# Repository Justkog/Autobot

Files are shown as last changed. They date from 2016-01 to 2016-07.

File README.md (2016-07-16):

# Autobot
42 Project

This repo regroups code and design documents created to build a robot with 3 microphones constantly listening to the environment. 
On detection of a sound, the robot performs a triangulation to locate the source and then goes towards it. 

Usage of Arduino or any similar board was not allowed.

We used a PIC32MX programmed via MPLABX. 
The PCB design was performed with Altium.

This project is not actively maintained.

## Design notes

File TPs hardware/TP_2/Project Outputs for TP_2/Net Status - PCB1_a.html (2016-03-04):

Altium customize

# Net Status Report

Date | : | 3/4/2016
Time | : | 4:05:06 PM
Elapsed Time | : | 00:00:00
Filename | : | C:\Users\bocal\Desktop\Autobot\TP_2\PCB1_a.PcbDoc
Units | : | mmmils

Nets | Layer | Length
ALIM | Signal Layers Only | 22.066mm
BATTERY | Signal Layers Only | 5.3418mm
GND | Signal Layers Only | 232.2898mm
LED0 | Signal Layers Only | 31.5226mm
LED1 | Signal Layers Only | 33.7189mm
LED2 | Signal Layers Only | 36.8631mm
LED3 | Signal Layers Only | 41.149mm
MCLR | Signal Layers Only | 13.7259mm
NetC10_2 | Signal Layers Only | 87.1646mm
NetD1_LED0_1 | Signal Layers Only | 1.9975mm
NetD1_LED1_1 | Signal Layers Only | 1.9975mm
NetD1_LED2_1 | Signal Layers Only | 1.9975mm
NetD1_LED3_1 | Signal Layers Only | 1.9975mm
NetD3_1 | Signal Layers Only | 2.8349mm
NetR2_2 | Signal Layers Only | 46.7649mm
PGC | Signal Layers Only | 31.7797mm
PGD | Signal Layers Only | 24.035mm
V3P3 | Signal Layers Only | 90.5993mm
V3P3A | Signal Layers Only | 67.5572mm
V5 | Signal Layers Only | 112.5743mm
X1 | Signal Layers Only | 20.602mm
X2 | Signal Layers Only | 41.4529mm

Back to top

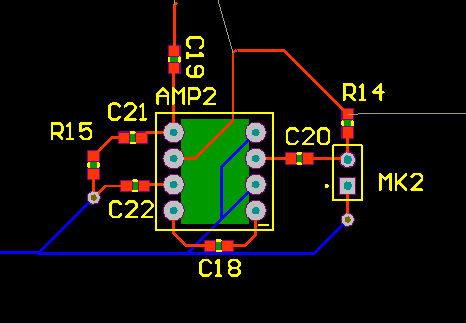
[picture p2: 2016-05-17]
Project Prototype/Amp.PNG

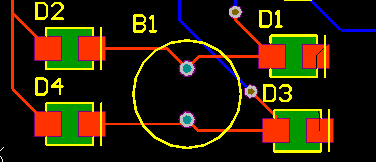
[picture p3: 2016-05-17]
Project Prototype/otor.PNG

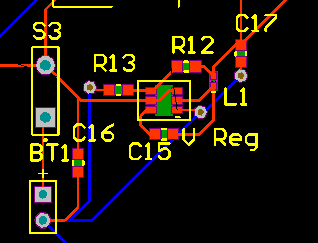
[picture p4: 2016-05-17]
Project Prototype/Alim.PNG

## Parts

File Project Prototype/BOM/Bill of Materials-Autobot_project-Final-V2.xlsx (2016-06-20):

Comment | Description | Footprint | LibRef | Quantity | Value | Fabricant | Fournisseur | RefFabricant | RefFournisseur | LogicalDesignator | Recu
LED green | Typical INFRARED GaAs LED | LED1608 | LED0 | 1 |  | KINGBRIGHT | Farnell | KP-1608MGC | 8529825 | D9
LED red | Typical INFRARED GaAs LED | LED1608 | LED0 | 1 |  | KINGBRIGHT | Farnell | KP-1608SURCK | 2290329 | D10
LM1086CS-3.3 |  | TO-263-3 | LM1086CS-3.3 | 1 |  | TEXAS INSTRUMENT | Farnell | LM1086CS-3.3/NOPB | 1469044 | V Reg

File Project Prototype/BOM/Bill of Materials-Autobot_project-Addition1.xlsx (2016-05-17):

Comment | Description | Footprint | LibRef | Quantity | Value | Fabricant | Fournisseur | RefFabricant | RefFournisseur | LogicalDesignator
LM386 |  | Ampli | LM386 | 1 |  | TEXAS INSTRUMENT | Farnell | LM386N-1/NOPB | 2496437 | AMP
Protoboard | Protoboard |  |  | 1 |  | KEMO ELECTRONIC | Farnell | E012 | 2503759

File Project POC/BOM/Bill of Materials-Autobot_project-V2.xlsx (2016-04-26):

Comment | Description | Footprint | LibRef | Quantity | Value | Fabricant | Fournisseur | RefFabricant | RefFournisseur | LogicalDesignator
SSM2167 |  |  | SSM2167 | 3 |  | ANALOG DEVICES | Farnell | SSM2167-1RMZ | 2067797
Diode | Default Diode | SMC | Diode | 8 |  | DIODES INC. | Farnell | MURS140-13-F | 1858656 | D1, D2, D3, D4, D5, D6, D7, D8
L298N |  | L298N | L298N | 1 |  | STMICROELECTRONICS | Farnell | L298N | 403295 | L298N
Mic2 | Microphone | PIN2 | Mic2 | 3 |  | PRO SIGNAL | Farnell | ABM-708-RC | 1736564 | MK1
SW-PB | Switch | SPST-2 | SW-PB | 1 |  | MULTICOMP | Farnell | R13-509B-05-BR | 1634685 | S2
FT232R |  |  | FT232R | 1 |  | MOLEX | Farnell | 22-27-2041 | 9731164 | UART
Adaptateur CI |  |  |  | 3 |  | CAPITAL ADVANCED | Farnell | 33010 | 1384010
Supports CI |  |  |  | 3 |  | TE CONNECTIVITY | Farnell | 1-1814655-1 | 1218869
Wires F/M |  |  |  | 2 |  | PRO SIGNAL | Farnell | PSG-JMP150MF | 2452749
Wires M/M |  |  |  | 1 |  | MULTICOMP | Farnell | MCBBJ65 | 2396146

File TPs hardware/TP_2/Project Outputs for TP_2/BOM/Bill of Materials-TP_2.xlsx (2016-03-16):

Comment | Description | Footprint | LibRef | Quantity | Value | Fabricant | Fournisseur | RefFabricant | RefFournisseur | Precision | LogicalDesignator
10uF | Capacitor | CAPC2012N | Cap | 4 | 10uF | TDK, [NoValue], TDK, [NoValue] | Farnell, [NoValue], Farnell, [NoValue] | C2012X5R0J106M/1.25, [NoValue], C2012X5R0J106M/1.25, [NoValue] | 2309029, [NoValue], 2309029, [NoValue] | 6,3V X5R | C1, C10, C12, C13
100nF | Capacitor | CAPC1608N | Cap | 7 | 100nF |  |  |  |  | 50V X5R | C2, C3, C4, C5, C6, C7, C15
20pF | Capacitor | CAPC1608N | Cap | 2 | 20pF |  |  |  |  | 50V X5R | C8, C9
1uF | Capacitor | CAPC1608N | Cap | 2 | 1uF |  |  |  |  | 6,3V X5R | C11, C14
GF1A | Default Diode | SMA/DO-214AC_21 | Diode | 2 |  | VISHAY | Farnell | GF1A-E3/67A | 9549560 |  | D1, D2
Green LED | Typical INFRARED GaAs LED, Typical INFRARED GaAs LED, Typical INFRARED GaAs LED, Typical INFRARED GaAs LED, Typical RED, GREEN, YELLOW, AMBER GaAs LED | LED 0805 | LED0, LED0, LED0, LED0, LED2 | 5 |  | KINGBRIGHT | Farnell | KPT-2012SGC | 2099239 |  | D1, D1, D1, D1, D3
600r | Inductor | INDC1608AN | Inductor | 1 | 600 | Wurth | Farnell | 742792651 | 1635706 |  | FB1
Program / Debug |  | RJ12_90 | Component_1 | 1 |  | Molex | Farnell | 53398-0671 | 1125368 |  | J1
12V Main | Header, 2-Pin | PHOENIX_1985195 | Header 2 | 1 |  | PHOENIX CONTACT | Farnell | PTSA 1.5/2-3,5-Z | 1792769 |  | P1
12V Battery | Header, 2-Pin | PHOENIX_1985195 | Header 2 | 1 |  | PHOENIX CONTACT | Farnell | PTSA 1.5/2-3,5-Z | 1792769 |  | P2
470r | Resistor | RESC1608N | Res1 | 1 | 470r |  |  |  |  |  | R1
330r | Resistor | RESC1608N | Res1 | 4 | 330r |  |  |  |  | 1% | R1
1K | Potentiometer | PDB181-K415K-102A2 | RPot | 1 | 1K | BOURNS | Farnell | PDB181-K415K-102A2 | 1823540 |  | R2
4.7K | Resistor | RESC1608N | Res1 | 1 | 4.7K |  |  |  |  | 1% | R3
PIC32MX764F128H |  | QFP50P1200X1200X120-64 | PIC32MX764F128H | 1 |  | Microchip | Farnell | PIC32MX764F128H | 1971889 |  | U1
AP1117 | 1A LDO, 18V input, DPAK | TD03B_N | AP1117 | 1 |  | DIODES INC | Farnell | AP1117D33G-13 | 1825285 |  | U2
8MHz | Crystal Oscillator | XTAL139X50X45 | XTAL | 1 |  | FOX ELECTRONICS | Farnell | FOXSDLF/080-20 | 2063972 |  | Y1

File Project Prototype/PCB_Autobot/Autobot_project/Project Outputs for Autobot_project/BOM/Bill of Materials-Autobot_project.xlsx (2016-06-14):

Comment | Description | Footprint | LibRef | Quantity | Value | Fabricant | Fournisseur | RefFabricant | RefFournisseur | LogicalDesignator
LM386 |  | Ampli | LM386 | 3 |  | TEXAS INSTRUMENT | Farnell | LM386N-1/NOPB | 2496437 | AMP
Motor | Motor, General Kind | BORNIER | Motor | 2 |  |  | Olimex |  |  | B1, B2
6V | Multicell Battery | BAT-2 | Battery | 1 | 6V |  | Olimex |  |  | BT1
0.1uF | Capacitor | CAPC1608N | Cap | 13 | 0.1uF |  |  |  |  | C1, C1, C1, C3, C3, C3, C5, C5, C5, C10, C12, C13, C14
10uF | Capacitor | CAPC1608N | Cap | 9 | 10uF |  |  |  |  | C2, C2, C2, C11, C16, C17, C18, C18, C18
47pF | Capacitor | CAPC1608N | Cap | 3 | 47pF |  |  |  |  | C4
Cap | Capacitor | CAPC1608N | Cap | 2 | 100nF |  |  |  |  | C6, C7
100nF | Capacitor | CAPC1608N | Cap | 2 | 100nF |  |  |  |  | C8, C9
22uF | Capacitor | CAPC1608N | Cap | 1 | 22uF |  |  |  |  | C15
Diode | Default Diode | DIODE | Diode | 8 |  | DIODES INC. | Farnell | MURS140-13-F | 1858656 | D1, D2, D3, D4, D5, D6, D7, D8
LED green | Typical INFRARED GaAs LED | LED1608 | LED0 | 1 |  | DIODES INC. | Farnell | MURS140-13-F | 1858656 | D9
LED red | Typical INFRARED GaAs LED | LED1608 | LED0 | 1 |  | DIODES INC. | Farnell | MURS140-13-F | 1858656 | D10
WS6F |  | 6-pin Connector | WS6F | 1 |  | MOLEX | Farnell | 22-11-2062 | 1462951 | ICSP
L298N |  | L298N | L298N | 1 |  | STMICROELECTRONICS | Farnell | L298N | 403295 | L298N
Mic | Microphone | BORNIER | Mic2 | 3 |  | PRO SIGNAL | Farnell | ABM-708-RC | 1736564 | MK1
PIC32MX250F128D |  | 44TQFP | PIC32MX250F128D | 1 |  | MICROCHIP | Farnell | PIC32MX250F128D-50I-PT | 2357347 | PIC
10KR | Resistor | RESC1608N | Res1 | 4 | 10KR |  |  |  |  | R1, R1, R1, R3
10R | Resistor | RESC1608N | Res1 | 3 | 10R |  |  |  |  | R2
1KR | Resistor | RESC1608N | Res1 | 1 | 1KR |  |  |  |  | R4
300KR | Resistor | RESC1608N | Res1 | 3 | 300KR |  |  |  |  | R5
330R | Resistor | RESC1608N | Res1 | 4 | 330R |  |  |  |  | R6, R7, R9, R11
10K | Resistor | RESC1608N | Res1 | 2 | 10K |  |  |  |  | R8, R10
430KR | Resistor | RESC1608N | Res1 | 3 | 430KR |  |  |  |  | R14
SW-PB | Switch | SPST-2 | SW-PB | 3 |  | MULTICOMP | Farnell | R13-509B-05-BB, R13-509B-05-BR, R13-608C1-02-BB-9A | 1634683, 1634685, 1634617 | S1, S2, S3
FT232R |  | 6-pin Connector | FT232R | 1 |  | MOLEX | Farnell | 22-27-2041 | 9731164 | UART
LM1117SX-3.3 |  | TO-263-3 | LM1117SX-3.3 | 1 |  | TEXAS INSTRUMENT | Farnell | LM1117SX-3.3/NOPB | 2323594 | V Reg

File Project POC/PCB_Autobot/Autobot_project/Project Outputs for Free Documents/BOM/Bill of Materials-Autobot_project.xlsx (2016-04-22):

Comment | Description | Footprint | LibRef | Quantity | Value | Fabricant | Fournisseur | RefFabricant | RefFournisseur | LogicalDesignator
SSM2167 |  |  | SSM2167 | 3 |  | ANALOG DEVICES | Farnell | SSM2167-1RMZ | 2067797
Motor | Motor, General Kind | RB5-10.5 | Motor | 2 |  |  | Olimex |  |  | B1, B2
10uF | Capacitor | RAD-0.3 | Cap | 12 | 10uF |  |  |  |  | C1, C1, C1, C2, C2, C2, C3, C3, C3, C5, C5, C5
0.1uF | Capacitor | RAD-0.3 | Cap | 3 | 0.1uF |  |  |  |  | C4
Cap | Capacitor | RAD-0.3 | Cap | 2 | 100nF |  |  |  |  | C6, C7
100nF | Capacitor | RAD-0.3 | Cap | 2 | 100nF |  |  |  |  | C8, C9
Diode | Default Diode | SMC | Diode | 8 |  | DIODES INC. | Farnell | MURS140-13-F | 1858656 | D1, D2, D3, D4, D5, D6, D7, D8
LED green | Typical INFRARED GaAs LED | LED-0 | LED0 | 1 |  | DIODES INC. | Farnell | MURS140-13-F | 1858656 | D9
LED red | Typical INFRARED GaAs LED | LED-0 | LED0 | 1 |  | DIODES INC. | Farnell | MURS140-13-F | 1858656 | D10
L298N |  | L298N | L298N | 1 |  | STMICROELECTRONICS | Farnell | L298N | 403295 | L298N
Mic2 | Microphone | PIN2 | Mic2 | 3 |  | PRO SIGNAL | Farnell | ABM-708-RC | 1736564 | MK1
0R | Resistor | AXIAL-0.3 | Res1 | 3 | 0R |  |  |  |  | R1
2KR | Resistor | AXIAL-0.3 | Res1 | 3 | 2KR |  |  |  |  | R2
500KR | Resistor | AXIAL-0.3 | Res1 | 3 | 500KR |  |  |  |  | R3
100KR | Resistor | AXIAL-0.3 | Res1 | 3 | 100KR |  |  |  |  | R4
Res1 | Resistor | AXIAL-0.3 | Res1 | 1 | 0 |  |  |  |  | R5
330R | Resistor | AXIAL-0.3 | Res1 | 4 | 330R |  |  |  |  | R6, R7, R9, R11
10K | Resistor | AXIAL-0.3 | Res1 | 2 | 10K |  |  |  |  | R8, R10
SW-PB | Switch | SPST-2 | SW-PB | 2 |  | [NoValue], MULTICOMP | Farnell | [NoValue], R13-509B-05-BR | [NoValue], 1634685 | S1, S2
PIC32MX340F512H |  |  | PIC32MX340F512H | 1 |  |  | Farnell |  |  | U*
FT232R |  |  | FT232R | 1 |  | MOLEX | Farnell | 22-27-2041 | 9731164 | UART

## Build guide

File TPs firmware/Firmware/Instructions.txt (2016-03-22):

Le TP se déroule en étapes, à faire valider à chaque fois :

0/ Boot from scratch

Créer un nouveau projet et y ajouter un nouveau .h contenant des typedefs pour :
- u8, u16 et u32
- s8, s16 et s32

1/ Commande de la LED par le bouton (a.k.a Hello World!)

Une pression sur le bouton allume la led
Une autre pression sur le bouton éteint la led

2/ Clignotement de la LED

La led clignotte au rythme d'un changement d'état par seconde (0.5Hz, 1s on/1s off).
Une pression sur le bouton multiplie par deux le rythme de clignotement. Arrivé à 8Hz, une pression sur le bouton remet le rythme à 0.5Hz.

La "séquence" sera donc : 0.5Hz, 1Hz, 2Hz, 4Hz, 8hZ, 0.5Hz, 1Hz, ...

Vous devez utiliser un timer pour régler la vitesse de clignotement

3/ Utilisation des interruptions

Votre code doit maintenant être "non bloquant", votre main loop ne doit contenir qu'un statement: clear watchdog
Le clignotement ainsi que la gestion du bouton doivent être fait dans une ISR.

4/ DIM de la LED (a.k.a pour-les-vrais-qui-en-ont-dans-le-slip-ou-le-string)

Votre code fait toujours la même chose, mais sur un appui long (>2s) la led passe en mode DIM, en 5s son intensité passe de 0 à 100% puis de 100% à 0% (et ainsi de suite)

Pour cela vous coderez en firmware un PWM sur la GPIO qui contrôle la LED.

5/ Ca y est, vous savez tout faire, elle est pas belle la vie ?

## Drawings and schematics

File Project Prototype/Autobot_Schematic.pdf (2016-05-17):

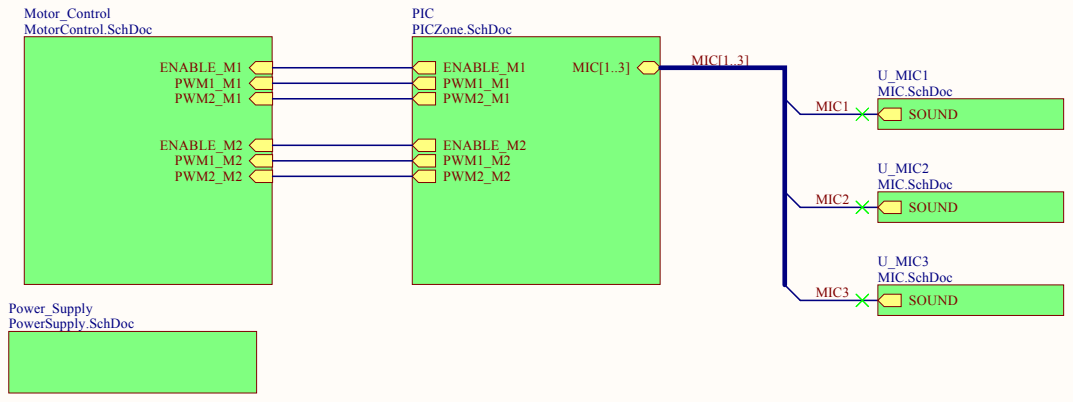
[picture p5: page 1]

Title Main | Autobot Limited 96, boulevard Bessiere 75017 PARIS

Size: A4 | Number: | Revision:
Date: 5/17/2016 Time: 10:52:24 PM | | Sheet of

C:\Users\bocal\Desktop\Autobot\Project Prototype\PCB_Autobot\Autobot_project\MicsBus.SchDoc
File:

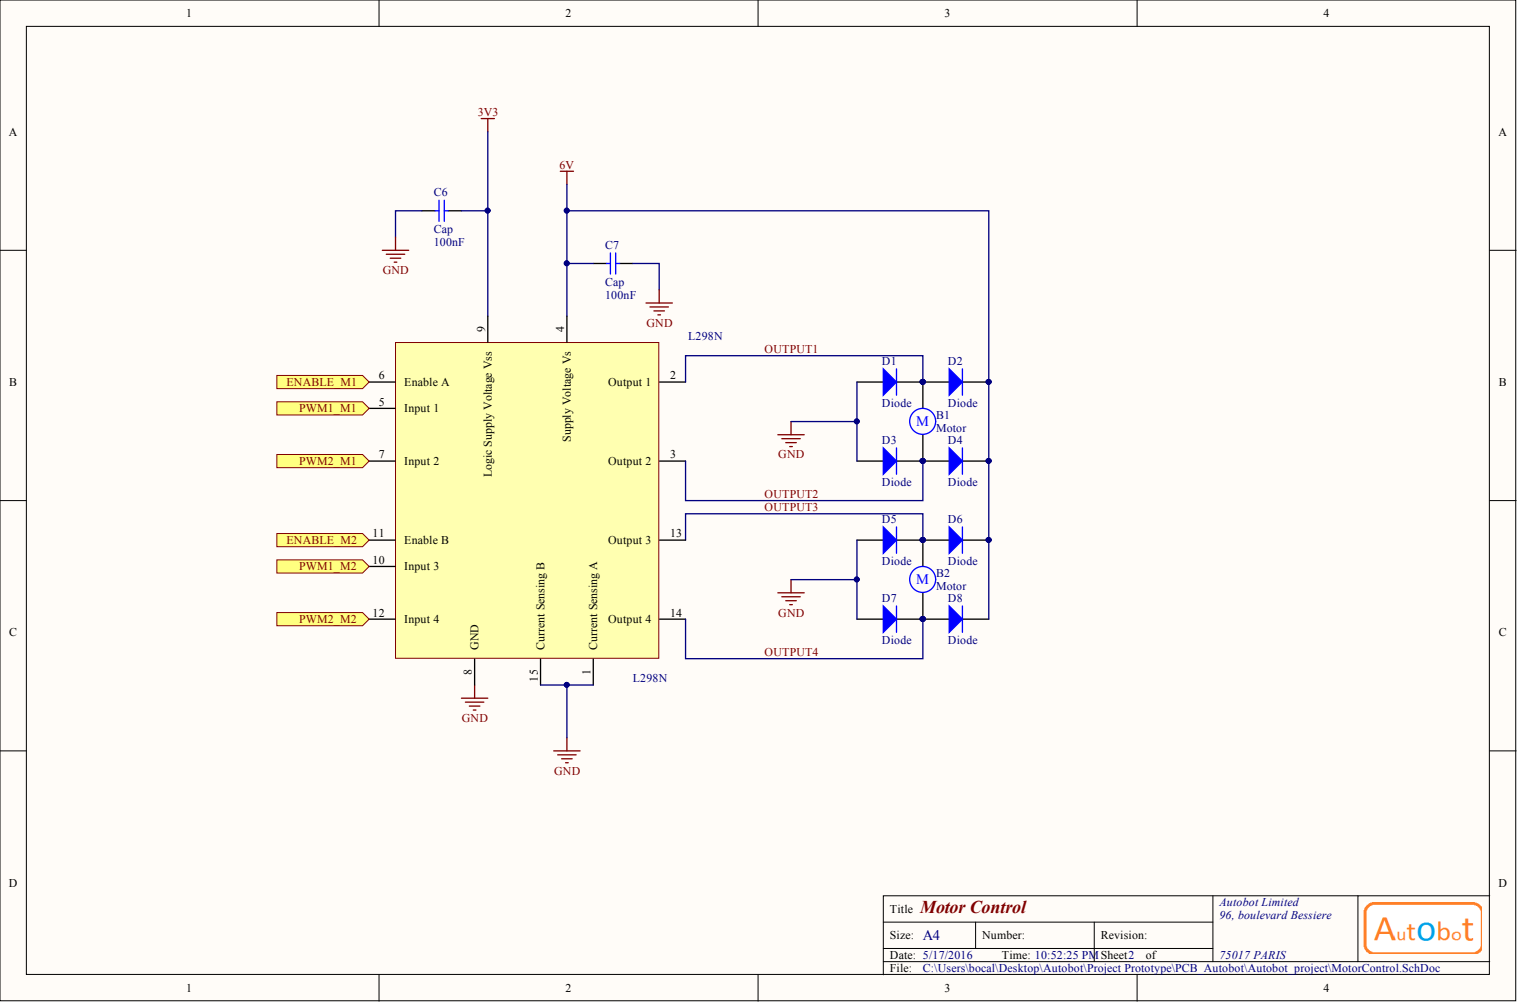
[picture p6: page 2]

Logic Supply Voltage Vss 9

C:\Users\bocal\Desktop\Autobot\Project Prototype\PCB_Autobot\Autobot_project\MotorControl.SchDoc

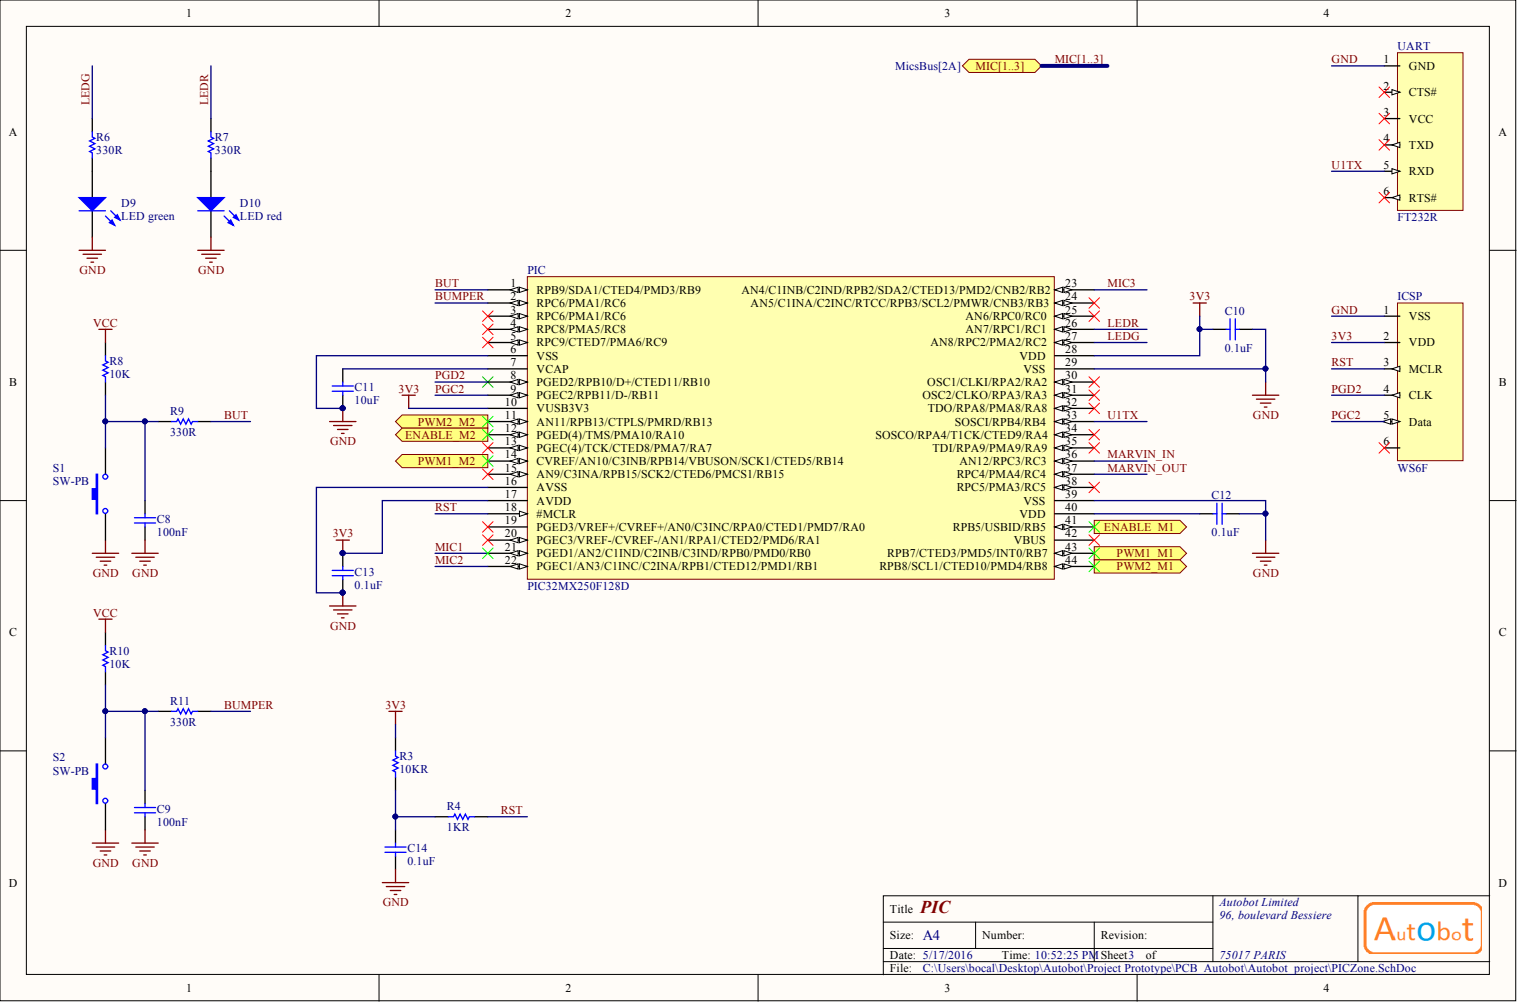
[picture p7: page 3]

T i t l e | A u t o b o t Li m i ted 9 6, b o u leva r d Bes s ier e 7 PA RIS

Size: A | N umber: | Rev i s i o n :

T ime: : : 5 PM | | Sheet o f

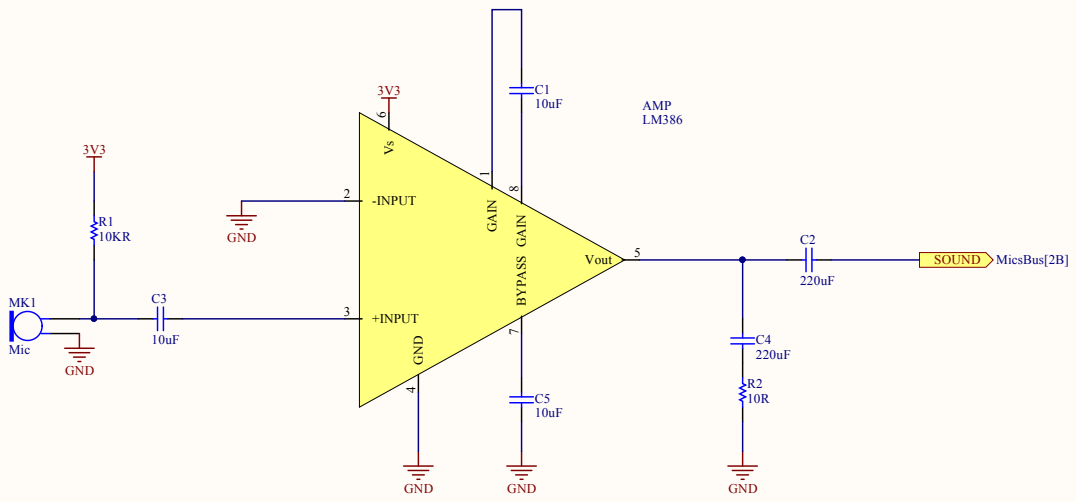
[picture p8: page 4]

C:\Users\bocal\Desktop\Autobot\Project Prototype\PCB_Autobot\Autobot_project\MIC.SchDoc

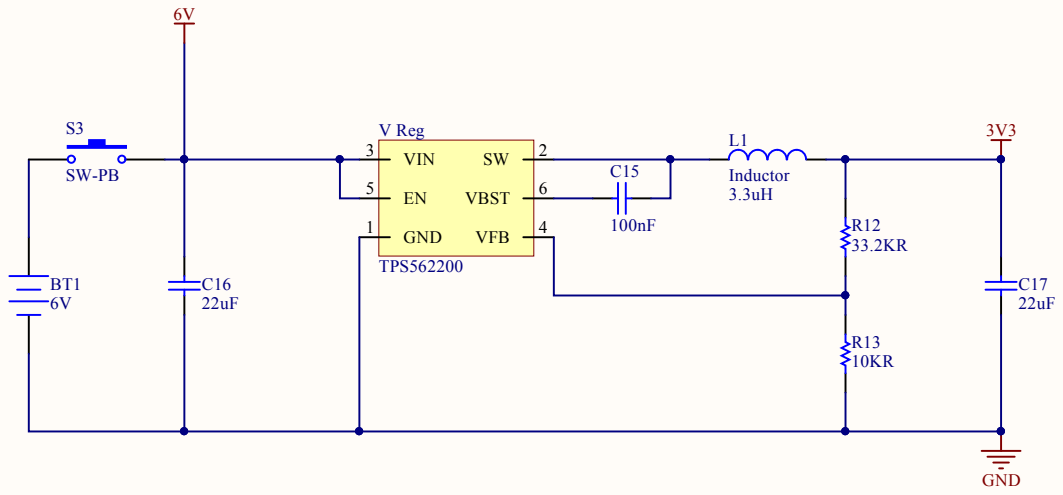
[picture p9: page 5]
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

Size: A | N umber: | Rev i s i o n :

/ / T ime: : : 5 PM | | Sheet o f

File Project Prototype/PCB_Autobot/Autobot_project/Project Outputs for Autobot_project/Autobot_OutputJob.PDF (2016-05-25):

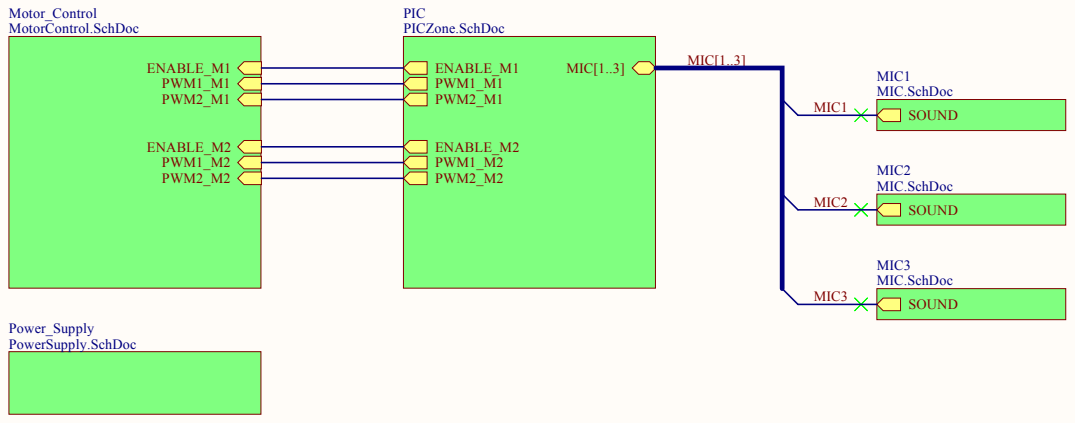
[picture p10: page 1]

Title Main | Autobot Limited 96, boulevard Bessiere 75017 PARIS

Size: A4 | Number: | Revision:
Date: 5/25/2016 Time: 8:50:44 PM | | Sheet of

C:\Users\bocal\Desktop\Autobot\Project Prototype\PCB_Autobot\Autobot_project\MicsBus.SchDoc
File:

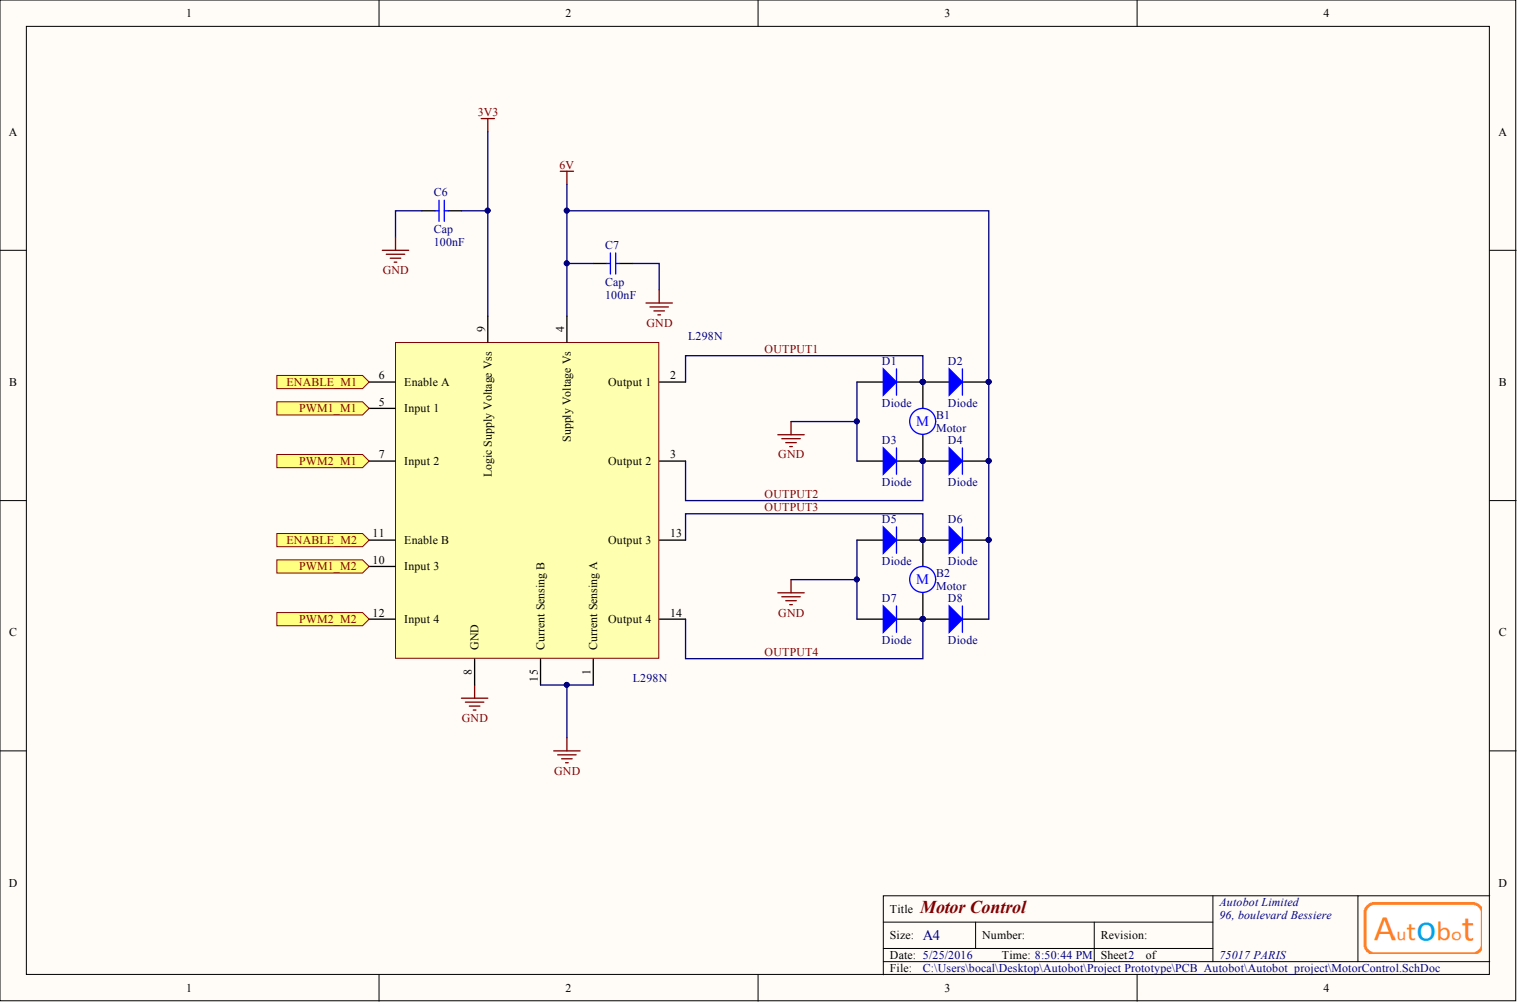
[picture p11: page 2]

Logic Supply Voltage Vss 9

Title Motor Control | Autobot Limited 96, boulevard Bessiere 75017 PARIS

Size: A4 | Number: | Revision:
5/25/2016 Time: 8:50:44 PM | | Sheet of

C:\Users\bocal\Desktop\Autobot\Project Prototype\PCB_Autobot\Autobot_project\MotorControl.SchDoc
File:

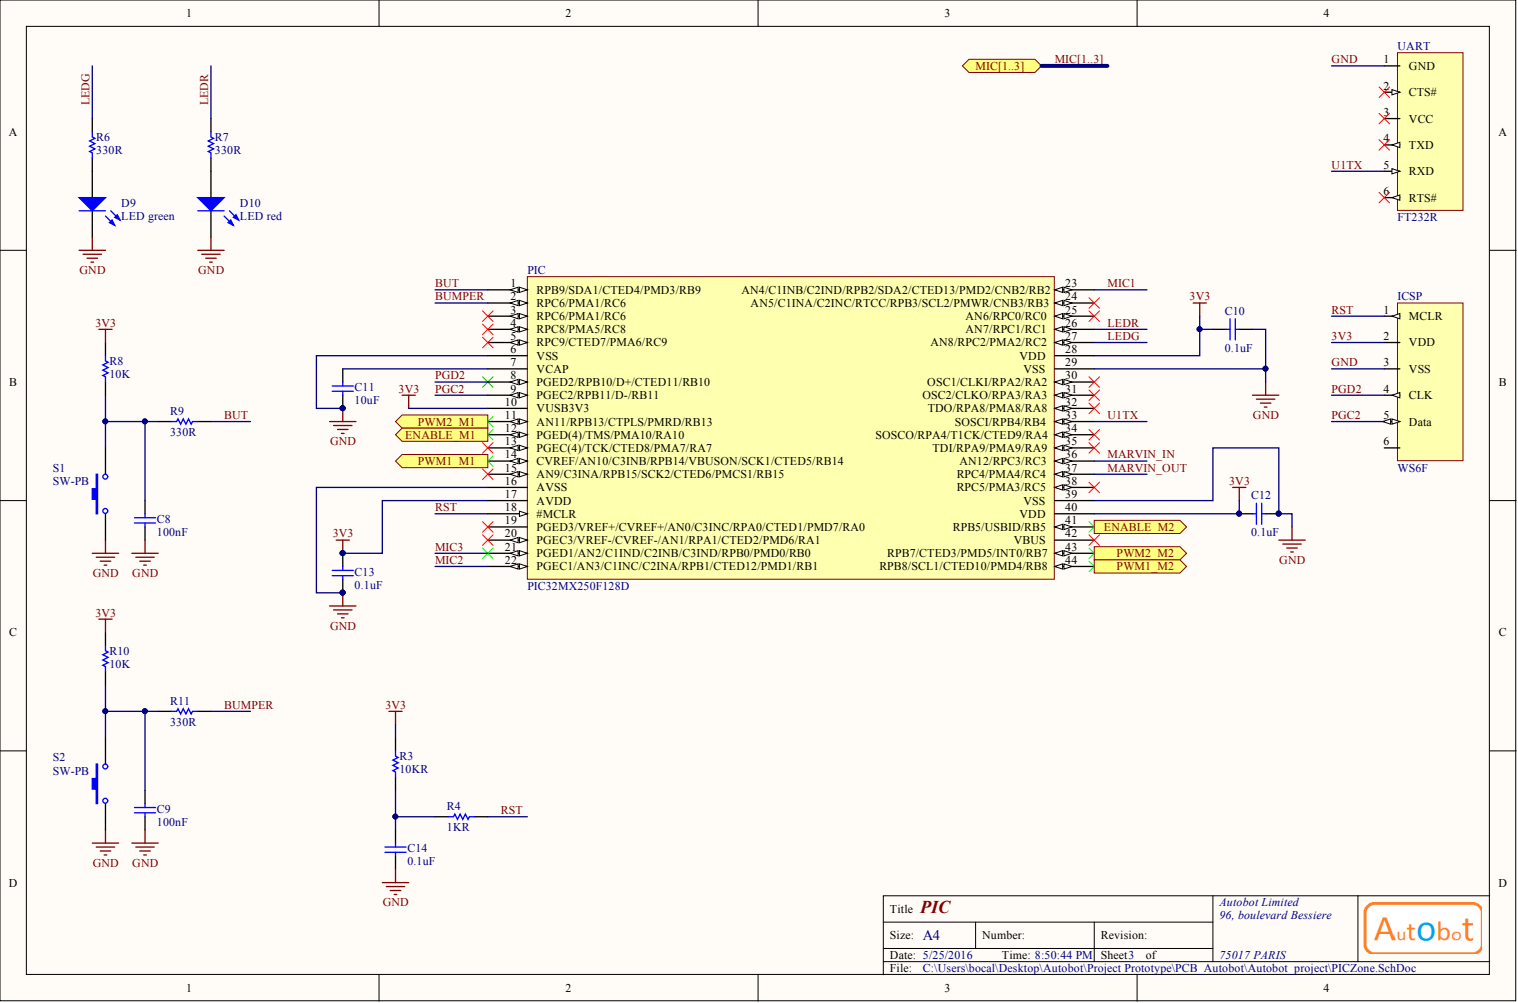
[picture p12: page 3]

T i t l e | A u t o b o t Li m i ted 9 6, b o u leva r d Bes s ier e 7 PA RIS

Size: A | N umber: | Rev i s i o n :

T ime: : : 4 PM | | Sheet o f

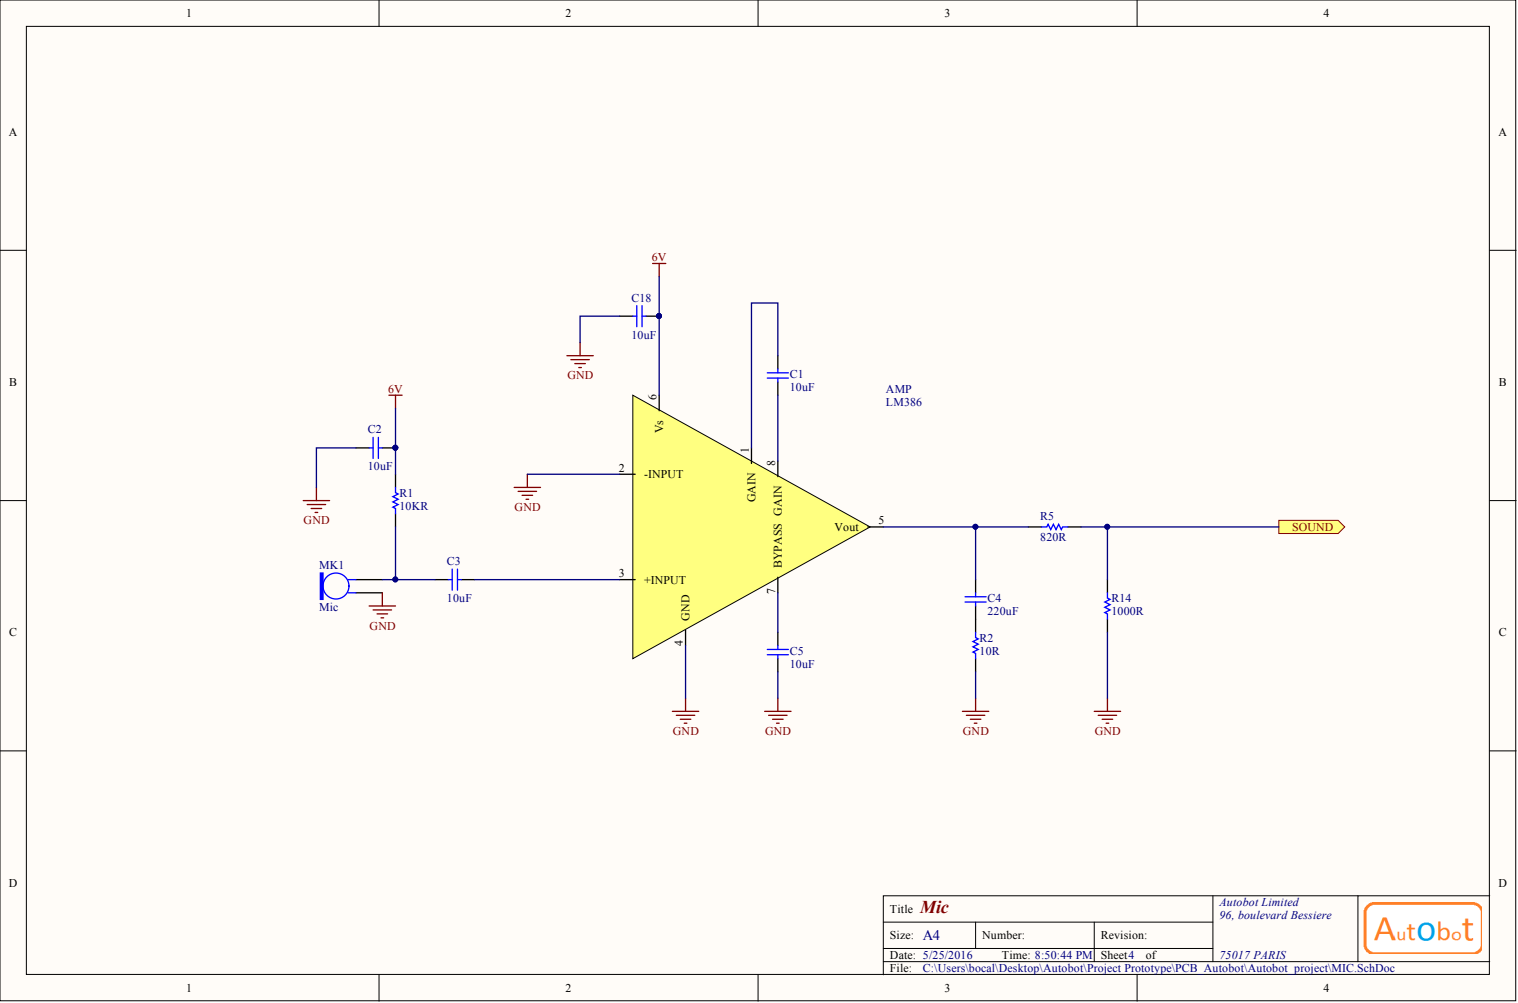
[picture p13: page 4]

Title Mic | Autobot Limited 96, boulevard Bessiere 75017 PARIS

Size: A4 | Number: | Revision:
5/25/2016 Time: 8:50:44 PM | | Sheet of

C:\Users\bocal\Desktop\Autobot\Project Prototype\PCB_Autobot\Autobot_project\MIC.SchDoc
File:

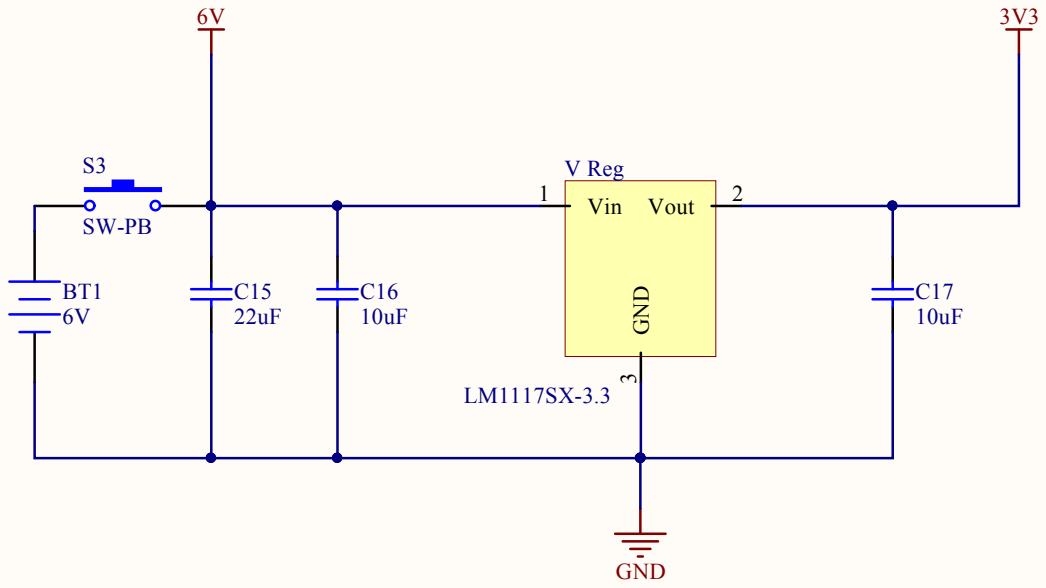
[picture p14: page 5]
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

Size: A | N umber: | Rev i s i o n :

/ / T ime: : : 4 PM | | Sheet o f

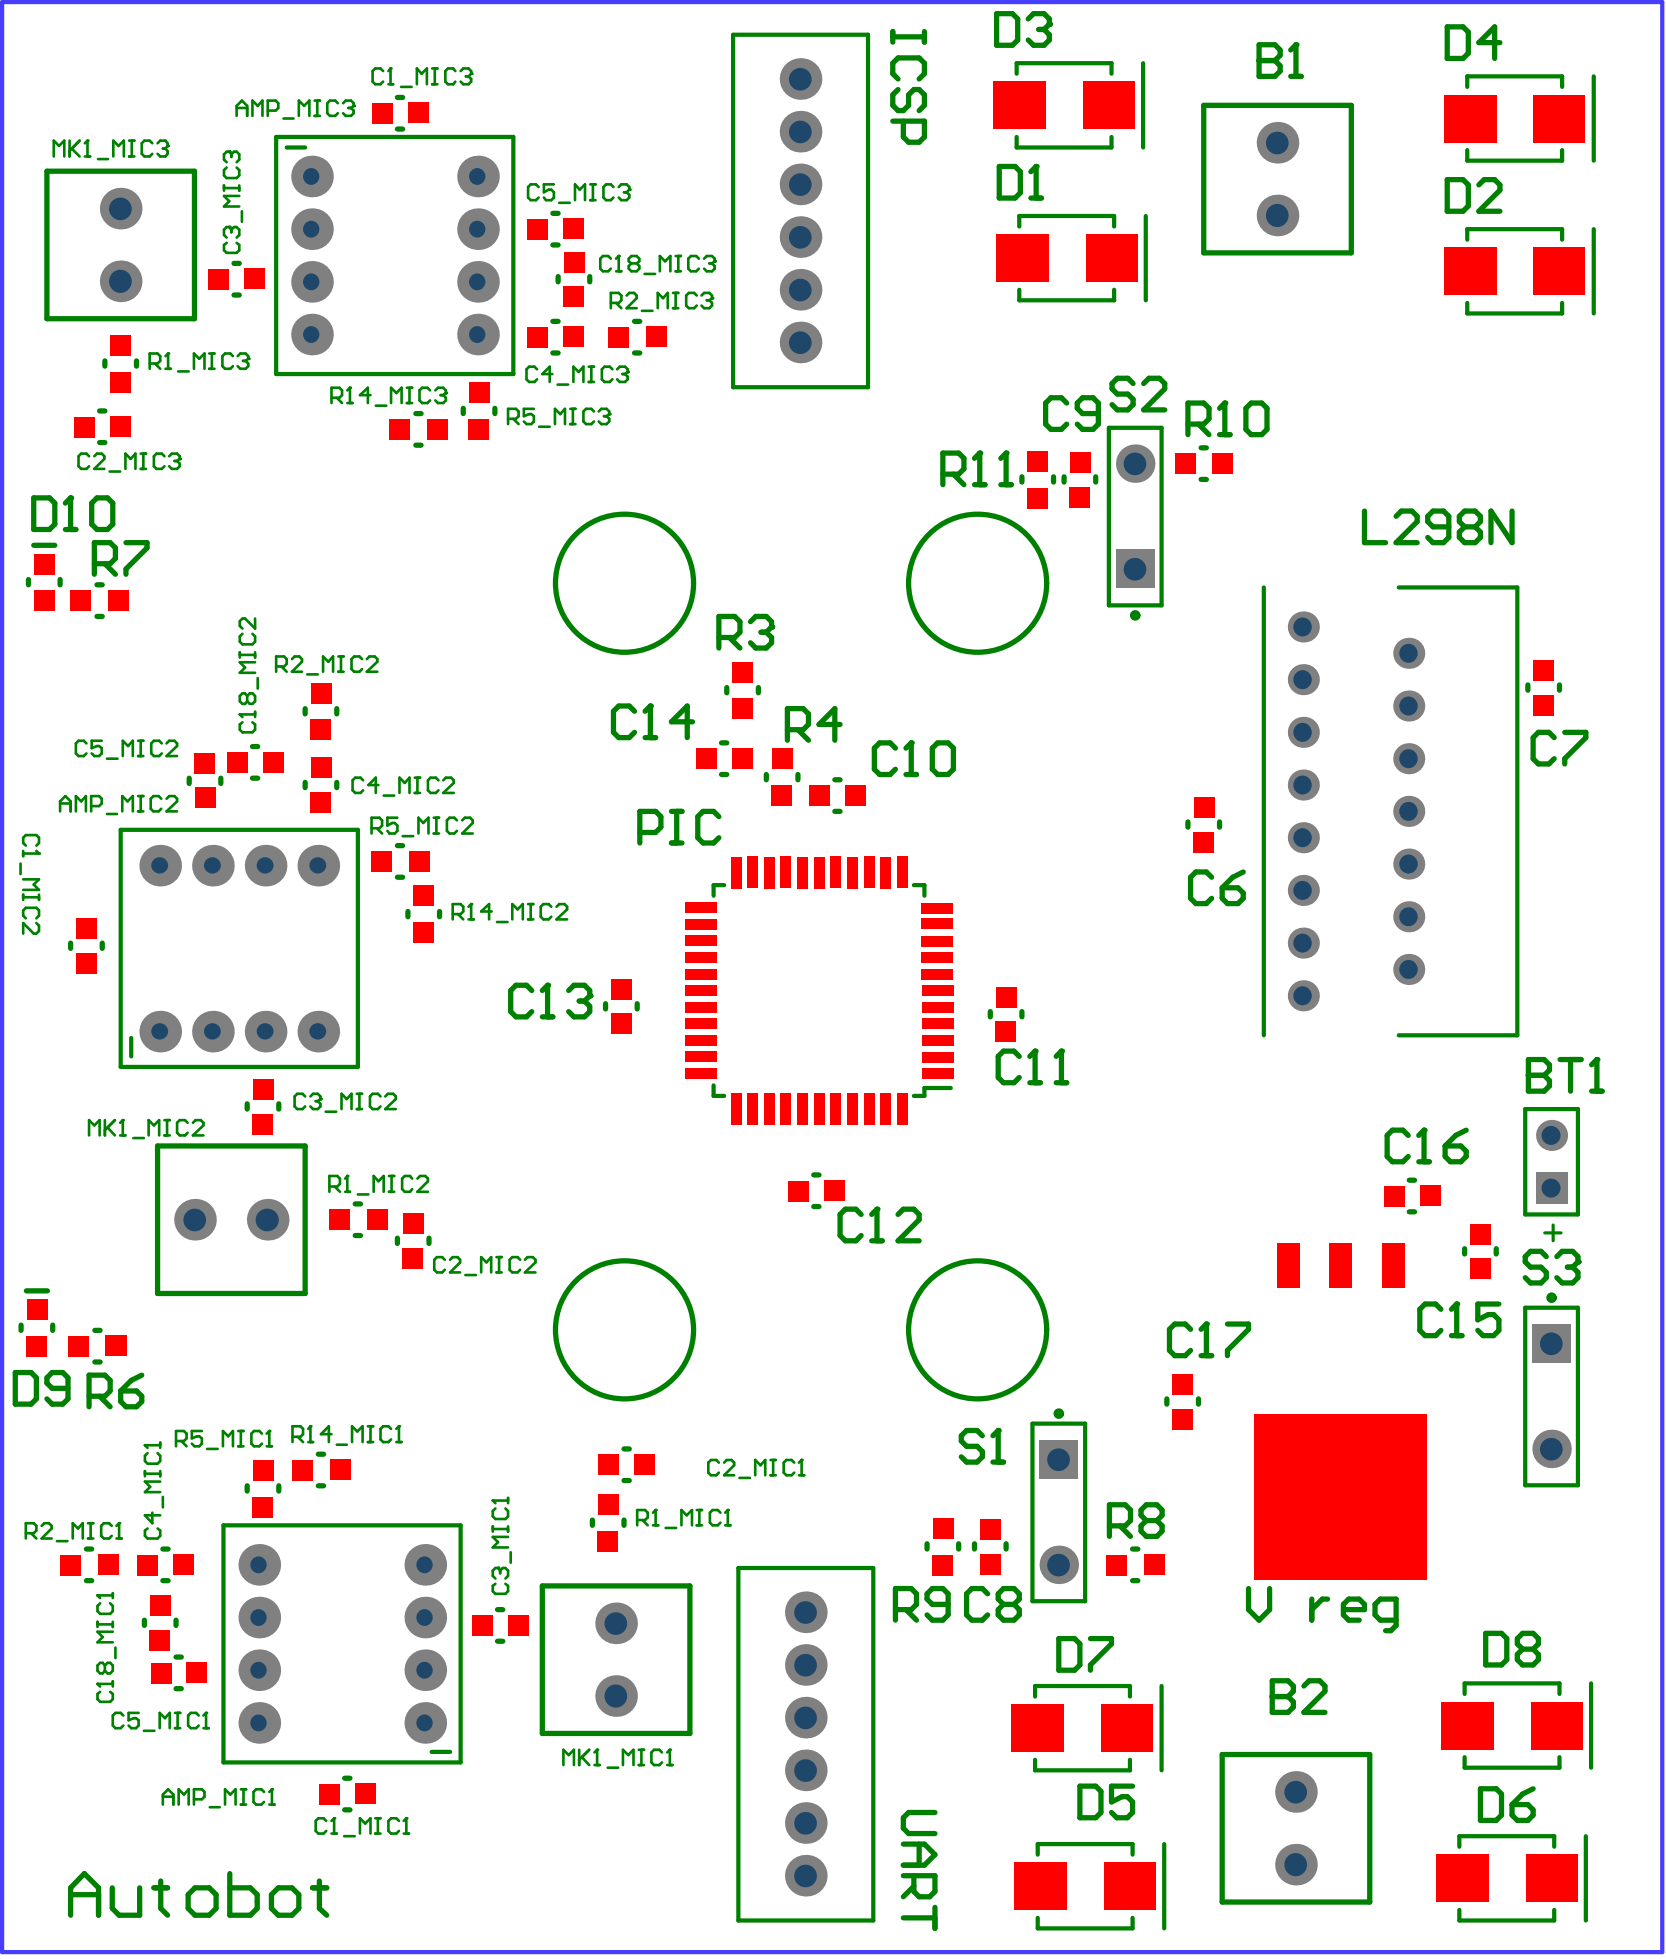
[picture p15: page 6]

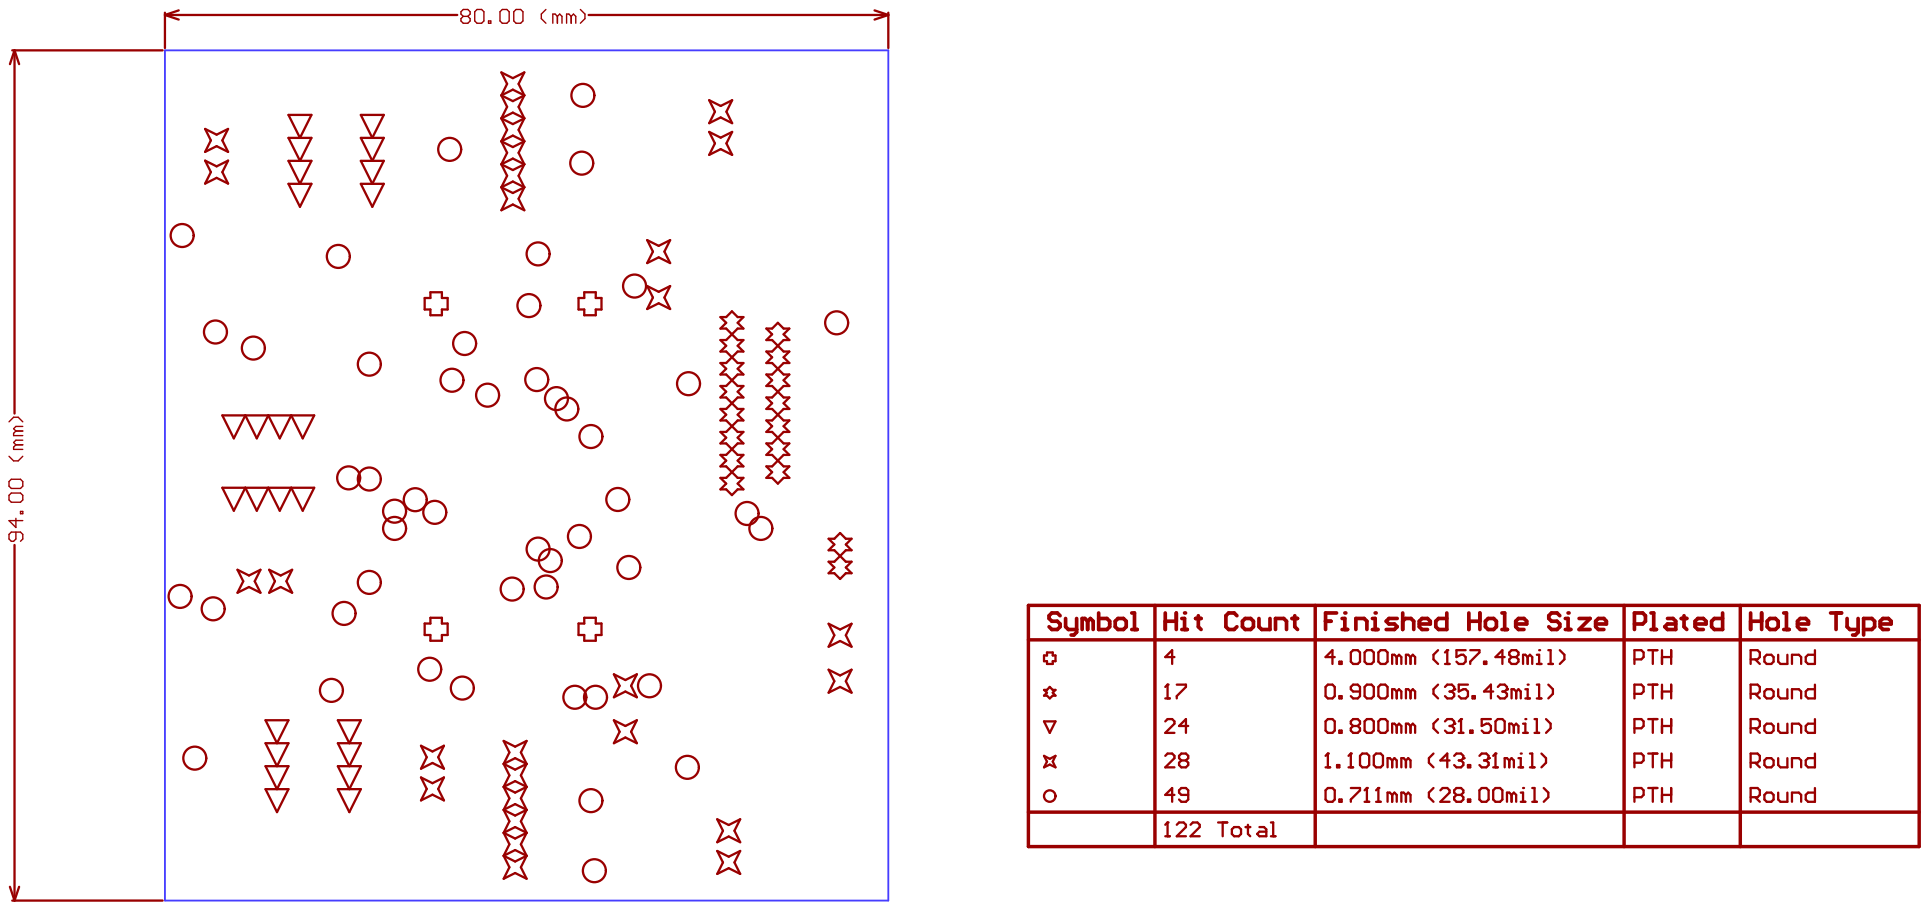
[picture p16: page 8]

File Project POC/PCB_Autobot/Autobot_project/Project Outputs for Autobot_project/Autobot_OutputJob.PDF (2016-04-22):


Title Main | Autobot Limited 96, boulevard Bessiere 75017 PARIS

Size: A4 | Number: | Revision:
Date: 4/22/2016 Time: 6:41:14 PM | | Sheet of

C:\Users\bocal\Desktop\Autobot\Project\PCB_Autobot\Autobot_project\MicsBus.SchDoc
File:


Logic Supply Voltage Vss 9

C:\Users\bocal\Desktop\Autobot\Project\PCB_Autobot\Autobot_project\MotorControl.SchDoc


T i t l e | A u t o b o t Li m i ted 9 6, b o u leva r d Bes s ier e 7 PA RIS

Size: A | N umber: | Rev i s i o n :

T ime: : : 4 PM | | Sheet o f


SHUTDOWN 3 INPUT 5

C:\Users\bocal\Desktop\Autobot\Project\PCB_Autobot\Autobot_project\MIC.SchDoc








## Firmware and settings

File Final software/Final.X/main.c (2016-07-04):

/* 
 * File:   main.c
 * Author: bocal
 *
 * Created on June 27, 2016, 12:28 AM
 */

#include "autobot.h"

void    pic_init(void)
{
    // initialiser tous les registres qui seront utilises
        // setup des GPIO (General Purpose Input Output)
            // les TRIS definissent la direction du pin
            // les LAT definissent l'etat du pin
    
    // LED en output
    LATCbits.LATC2 = 1;
    ANSELCbits.ANSC2 = 0;   // set pin mode to digital (0 = digital, 1 = analogic)
    TRISCbits.TRISC2 = 0;   // 0 = output
}

void    Stop_Green_Led(void)
{
    LATCbits.LATC2 = 0;
}

void    Start_Green_Led(void)
{
    LATCbits.LATC2 = 1;
}

void    Switch_Green_Led(void)
{
    LATCbits.LATC2 = LATCbits.LATC2 ^ 1;
}

int main()
{
    pic_init();
    logging_init();
    button_init();
    bumper_init();
    pwm_init();
    motor_timer_init();
    button_timer_init();
    sound_config_timer_init();

    //put_str_ln("Initialising DMA...");
    //init_DMA();

    //put_str_ln("Initialising ADC...");
    init_ADC();

    // setup des interrupts
    INTCONSET = _INTCON_MVEC_MASK;
    __builtin_enable_interrupts();

    if (VERBOSE_PIC_STATUS)
        put_str_ln("Ready.");

    while (1)
    {
        WDTCONbits.WDTCLR = 1;  // ecrire un 1 dans ce bit force la reinitialisation du watchdog
    }
}

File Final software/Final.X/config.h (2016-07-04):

/* 
 * File:   config.h
 * Author: Autobots
 *
 * Created on July 1, 2016, 6:07 PM
 */

# define LOG_BUFFER_SIZE                2048

# define PRIORITY_MOTOR                 7
# define PRIORITY_MIC                   6
# define PRIORITY_UART                  5

# define SUBPRIORITY_EMERGENCY          3

# define MOTOR_PWM_PERIOD               1024

# define MOTOR_1_GEAR_1_HANDICAP        920
# define MOTOR_1_GEAR_2_HANDICAP        970
# define MOTOR_1_GEAR_3_HANDICAP        970
# define MOTOR_2_GEAR_1_HANDICAP        1000
# define MOTOR_2_GEAR_2_HANDICAP        1000
# define MOTOR_2_GEAR_3_HANDICAP        1000

# define ACTION_TABLE_MAX_LENGTH        32
# define EMERGENCY_STOP_BACKWARD_DELAY  500
# define NEW_RECORD_DELAY               2000
# define SIXTY_DEGREES_TURN_DELAY       300             //25 * TICK_DELAY_FACTOR
# define TICK_DELAY_FACTOR              12              // SIXTY_DEGREES_TURN_DELAY / 25
# define SIDE_SWIM_DELAY                600

# define MOVEMENT_ACTIVATED             1

# define SOUND_AVERAGE_VALUE_COUNT      128
# define SOUND_THRESHOLD                75
# define MIC_ADC_TICKS_DISTANCE         25

# define SOUND_THRESHOLD_1              100
# define SOUND_THRESHOLD_2              115
# define SOUND_THRESHOLD_3              130
# define SOUND_THRESHOLD_4              150
# define SOUND_THRESHOLD_5              200

# define SOUND_BUFFER_SIZE              64

# define BATTERY_LEVEL_100_MIC3_AVG     (-65 * 128)
# define BATTERY_LEVEL_75_MIC3_AVG     (-75 * 128)
# define BATTERY_LEVEL_50_MIC3_AVG     (-90 * 128)
# define BATTERY_LEVEL_25_MIC3_AVG     (-110 * 128)

# define VERBOSE_PIC_STATUS             1
# define VERBOSE_MOTOR_HARDWARE         1
# define VERBOSE_MOTOR_SOFTWARE         1
# define VERBOSE_MIC_HARDWARE           1
# define VERBOSE_MIC_SOFTWARE           1

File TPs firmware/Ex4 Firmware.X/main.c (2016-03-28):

/* 
 * File:   main.c
 * Author: bocal
 *
 * Created on March 23, 2016, 7:46 PM
 */

#include <p32xxxx.h>
#include <sys/attribs.h>
#include "types.h"

u16 g_divider = 1;
u16 g_timer3_ended = 1;
u16 g_pwm = 0;
u8  g_pwm_mode = 0;
u8  g_pwm_up = 1;

void __ISR(_TIMER_2_VECTOR, IPL7SRS) timerHANDLER(void)
{
    if (!g_pwm_mode)
    {
        if (LATFbits.LATF1 == 1)
            LATFbits.LATF1 = 0;
        else
            LATFbits.LATF1 = 1;
    }
    else
    {
        if (g_pwm_up)
        {
            if (g_pwm < 50)
                g_pwm++;
            else
                g_pwm_up = 0;
        }
        else
        {
            if (g_pwm > 1)
                g_pwm--;
            else
                g_pwm_up = 1;
        }
    }
    IFS0bits.T2IF = 0;              // Clearing Timer2 interrupt flag
}

void __ISR(_TIMER_4_VECTOR, IPL7SRS) timer4HANDLER(void)
{
    if (LATFbits.LATF1 == 1)
    {
        TMR4 = g_pwm * 61;
        LATFbits.LATF1 = 0;
    }
    else
    {
        TMR4 = PR4 - g_pwm * 62;
        LATFbits.LATF1 = 1;
    }

    IFS0bits.T4IF = 0;              // Clearing Timer4 interrupt flag
}

void __ISR(_TIMER_3_VECTOR, IPL7SRS) timer3HANDLER(void)
{
    IEC0bits.T3IE = 0;              // desactivate interrupt
    T3CON = 0x0;                    // clear timer
    TMR3 = 0x0;                     // reset timer start
    g_timer3_ended = 1;             // set timer 3 as ended

    if (PORTDbits.RD8 == 0)         // if the button is indeed still pushed
    {
        //start the software pwm shit with timer2 as reference (timer 2 will be executed 50 times in 5 sec

        IEC0bits.T2IE = 0;
        IFS0bits.T2IF = 0;
        T2CON = 0x0;
        TMR2 = 0x0;
        PR2 = 3125;                    // 8Mhz : 8 (peripheral clock divisor) : 32 (prescale) * 5 : 50
                                        // = 10 timer ticks per 5 sec
        T2CONbits.TCKPS = 0x5;        // 1:32 prescale value

        IFS0bits.T4IF = 0;
        T4CON = 0x0;
        TMR4 = 0x0;
        PR4 = 3101;                    // 8Mhz : 8 (peripheral clock divisor) : 1 (prescale)
        T4CONbits.TCKPS = 0x1;        // 1:2 prescale value
        IPC4bits.T4IP = 7;              // set priority

        IEC0bits.T4IE = 1;              // enable timer 4 interrupts
        IEC0bits.T2IE = 1;              // enable timer 2 interrupts

        T2CONbits.ON = 1;               // start timer
        T4CONbits.ON = 1;               // start timer

        g_pwm_mode = 1;
    }

    IFS0bits.T3IF = 0;              // reset the interrupt flag
}

void __ISR(_EXTERNAL_1_VECTOR, IPL4SOFT) buttonHANDLER(void)
{
    //check on timer 3 to make sure that we are not in push noise
    //if it is ON, it means that the button was just pushed
    if ((g_timer3_ended == 1) && INTCONbits.INT1EP == 0)
    {              
        g_divider = g_divider * 2;
        if (g_divider > 16)
            g_divider = 1;
        PR2 = 62500 / g_divider;
        
        //set rising edge external interrupt
        INTCONbits.INT1EP = 1;
        
        IFS0bits.T3IF = 0;              // clear interrupt
        g_timer3_ended = 0;             
        T3CON = 0x0;                    // clear timer
        TMR3 = 0x0;                     // set timer start
        T3CONbits.TCKPS = 0x5;          // 1:32 prescale value
        PR3 = 62500;                    // 2s (8 : 8 : 32 * 0.1)
        IPC3bits.T3IP = 7;              // set priority
        IEC0bits.T3IE = 1;              // start interrupt
        T3CONbits.ON = 1;               // start timer

        g_pwm_mode = 0;
    }
    else if (INTCONbits.INT1EP == 1)
    {
        IEC0bits.T3IE = 0;              // desactivate interrupt
        T3CON = 0x0;                    // clear timer
        TMR3 = 0x0;                     // reset timer start
        g_timer3_ended = 1;             // set timer 3 as already ended
        
        INTCONbits.INT1EP = 0;          // set falling edge external interrupt
    }

    IFS0bits.INT1IF = 0;
}

/*
 * 
 */

int main(void)
{
    //set high on LED pin as output value
    //LATFbits.LATF1 = 1;

    //set LED pin as output
    TRISFbits.TRISF1 = 0;

    //set BUT pin as input
    TRISDbits.TRISD8 = 1;

    T2CON = 0x0;
    TMR2 = 0x0;
    PR2 = 62500;                    // 8Mhz : 8 (peripheral clock divisor) : 16 (prescale)
                                    // = 62 500 timer ticks per sec
    
    T2CONbits.TCKPS = 0b100;        // 1:16 prescale value

    //setup INT1 to interrupt on falling edge
    INTCONbits.INT1EP = 0;

    //clear interrupt
    IFS0bits.T2IF = 0;
    IFS0bits.INT1IF = 0;

    //set priority
    IPC2bits.T2IP = 7;
    IPC1bits.INT1IP = 4;

    //starting interrupts  
    IEC0bits.T2IE = 1;
    IEC0bits.INT1IE = 1;

    INTCONSET = _INTCON_MVEC_MASK;
    __builtin_enable_interrupts();
    
    //start timer
    T2CONbits.ON = 1;

    //set timer 3 as already ended
    g_timer3_ended = 1;
    
    while (1)
    {
        WDTCONbits.WDTCLR = 1;
    }
    return (0);
}

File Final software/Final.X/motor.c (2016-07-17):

/*
 * File:   motor.c
 * Author: Autobots
 *
 * Created on June 21, 2016, 1:48 PM
 */

#include "autobot.h"

void    Stop_Bot(u16 arg);
void    Motor_Control_Stop(u16 delay_ms);

u8      save_available = 1;

// set motor handicap with mechanical testing to balance the manufacture differences
u16      motor_1_handicap[3] = {MOTOR_1_GEAR_1_HANDICAP, MOTOR_1_GEAR_2_HANDICAP, MOTOR_1_GEAR_3_HANDICAP};
u16      motor_2_handicap[3] = {MOTOR_2_GEAR_1_HANDICAP, MOTOR_2_GEAR_2_HANDICAP, MOTOR_2_GEAR_3_HANDICAP};

s8      motor_step = 1;
s8      motor_gear[7] = {-100, -80, -60, 0, 60, 80, 100};

u8      motor_gear_current_1 = 3;
u8      motor_gear_current_2 = 3;

u8      prev_motor_gear_current_1 = 3;
u8      prev_motor_gear_current_2 = 3;

u8      action_table_length = 0;
u8      action_table_index = 0;
void    (*action_table[ACTION_TABLE_MAX_LENGTH])(u16);
u16     action_table_arg[ACTION_TABLE_MAX_LENGTH];

u8      keep_rolling_mode = 0;          // Mode to listen while rolling
u8      flee_mode = 0;                  // Mode to flee the sound source
u8      auto_circle_mode = 0;           // Mode to circle infinitely in a threshold determined radius

u8      Is_Keep_Rolling_Mode(void)
{
    return (keep_rolling_mode);
}

void    Switch_Keep_Rolling_Mode(void)
{
    if (keep_rolling_mode)
        keep_rolling_mode = 0;
    else
        keep_rolling_mode = 1;
    if (VERBOSE_MOTOR_SOFTWARE)
        log_key_val("Keep Rolling Mode", keep_rolling_mode);
}

u8      Is_Flee_Mode(void)
{
    return (flee_mode);
}

void    Switch_Flee_Mode(void)
{
    if (flee_mode)
        flee_mode = 0;
    else
        flee_mode = 1;
    if (VERBOSE_MOTOR_SOFTWARE)
        log_key_val("Flee Mode", flee_mode);
}

u8      Is_Auto_Circle_Mode(void)
{
    return (auto_circle_mode);
}

void    Switch_Auto_Circle_Mode(void)
{
    if (auto_circle_mode)
        auto_circle_mode = 0;
    else
        auto_circle_mode = 1;
    if (VERBOSE_MOTOR_SOFTWARE)
        log_key_val("Auto Circle Mode", auto_circle_mode);
}

void    Reset_Motor_Instructions(void)
{
    if (VERBOSE_MOTOR_SOFTWARE)
        put_str_ln("Reset Motor Instructions");
    Motor_Control_Stop(0);
    u8      i = 0;
    while (i < ACTION_TABLE_MAX_LENGTH)
    {
        action_table[i] = 0;
        action_table_arg[i] = 0;
        i++;
    }
    action_table_index = 0;
    action_table_length = 0;
}

void    Add_Motor_Instruction(void (*action)(u16), u16 delay)
{
    if (action_table_length < ACTION_TABLE_MAX_LENGTH)
    {
        action_table[action_table_length] = action;
        action_table_arg[action_table_length] = delay;
        if (VERBOSE_MOTOR_SOFTWARE)
        {
            put_log("Action no ");
            put_log_nb(action_table_length);
            put_str_ln(" added");
        }
    }
    else
    {
        if (VERBOSE_MOTOR_SOFTWARE)
        {
            put_log("Action no ");
            put_log_nb(action_table_length);
            put_str_ln(" ignored");
        }
    }

    action_table_length++;
}

void    Execute_Motor_Instructions(void)
{
    if(action_table_index < ACTION_TABLE_MAX_LENGTH &&
            action_table[action_table_index])
    {
        Disable_ADC();
        if (VERBOSE_MOTOR_SOFTWARE)
            log_key_val("Execute instruction number", action_table_index);
        (*action_table[action_table_index])(action_table_arg[action_table_index]);
        action_table_index++;
    }
    else
    {
        Reset_Motor_Instructions();
        Enable_ADC();
    }
}

void    Motor_Save()
{
    if (save_available)
    {
        prev_motor_gear_current_1 = motor_gear_current_1;
        prev_motor_gear_current_2 = motor_gear_current_2;
        save_available = 0;
        if (VERBOSE_MOTOR_SOFTWARE)
            put_str_ln("Saving Motor Status");
    }
}

void    Motor_Restore()
{
    motor_gear_current_1 = prev_motor_gear_current_1;
    motor_gear_current_2 = prev_motor_gear_current_2;
    set_Motor_Speed();
    save_available = 1;
    Execute_Motor_Instructions();
    if (VERBOSE_MOTOR_SOFTWARE)
        put_str_ln("Restoring Motor Status");
}

void    Motor_Delay(u16 delay_ms)
{
    if (VERBOSE_MOTOR_SOFTWARE)
        log_key_val("Delay ", delay_ms);
    Start_Motor_Timer(delay_ms);
}

void    Motor_Control_Forward(u16 delay)
{
    if (motor_gear_current_1 == motor_gear_current_2)
    {
        if (motor_gear_current_1 < 6)
        {
            motor_gear_current_1++;
            motor_gear_current_2++;
        }
        set_Motor_Speed();
        if (VERBOSE_MOTOR_SOFTWARE)
            log_key_val("Forward to ", motor_gear_current_1);
    }
    Motor_Save();
    Motor_Delay(delay);
}

void    Motor_Control_Backward(u16 delay)
{
    if (motor_gear_current_1 == motor_gear_current_2)
    {
        if (0 < motor_gear_current_1)
        {
            motor_gear_current_1--;
            motor_gear_current_2--;

        }
        set_Motor_Speed();
        if (VERBOSE_MOTOR_SOFTWARE)
            log_key_val("Backward to ", motor_gear_current_1);
    }
    Motor_Save();
    Motor_Delay(delay);
}

void    Motor_Control_Emergency_Stop()
{
    if (VERBOSE_MOTOR_SOFTWARE)
        put_str_ln("/!\\ EMERGENCY STOP /!\\");
    motor_timer_init();
    Reset_Motor_Instructions();
    if (MOVEMENT_ACTIVATED)
    {
        Add_Motor_Instruction(Motor_Control_Backward, EMERGENCY_STOP_BACKWARD_DELAY);
        Add_Motor_Instruction(Motor_Control_Stop, 50);
        Add_Motor_Instruction(Motor_Control_Stop, 3000);
    }
    Add_Motor_Instruction(Stop_Bot, 0);
    Execute_Motor_Instructions();
}

void    Motor_Control_Stop(u16 delay_ms)
{
    if (VERBOSE_MOTOR_SOFTWARE)
        put_str_ln("Motor Status Save Overrided");
    if (delay_ms)
    {
        prev_motor_gear_current_1 = 3;
        prev_motor_gear_current_2 = 3;
        save_available = 0;
        Motor_Delay(delay_ms);
        if (VERBOSE_MOTOR_SOFTWARE)
            put_str_ln("stop with delay");
    }
    else
    {
        prev_motor_gear_current_1 = 3;
        prev_motor_gear_current_2 = 3;
        motor_gear_current_1 = 3;
        motor_gear_current_2 = 3;
        set_Motor_Speed();
        if (VERBOSE_MOTOR_SOFTWARE)
            put_str_ln("stop without delay");
        save_available = 1;
    }
}

void    Motor_Control_Turn_Left(u16 delay)
{
    Motor_Save();
    if (motor_gear_current_1 == motor_gear_current_2)
    {
        if (motor_gear_current_2 > 3)
            motor_gear_current_2--;
        else if (motor_gear_current_2 < 3)
            motor_gear_current_2++;
    }
    set_Motor_Speed();
    if (VERBOSE_MOTOR_SOFTWARE)
        put_str_ln("Turning left");
    Motor_Delay(delay);
}
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

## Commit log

2016-01-28 et merde
    [Sheet1.SchDoc, TP_1.PrjPcb]
2016-01-29 TP2 addition, WIP
    [PIC.SchDoc, Sheet1.SchDoc, TP2.SchDoc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]
2016-02-08 PIC addition + several component tags addition (fab, ref..)
    [PIC.SchDoc, Proram_debug.SchLib, TP2.SchDoc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]
2016-02-10 kiss my ass
    [Bill of Materials.xls, PcbLib1.PcbLib]
2016-02-15 Henrik and Vincent finnaly did it !
    [PcbLib1.PcbLib]
2016-02-19 update avec semiconducteursde controle moteur et ampli
    [MicroAmp.SchDoc, MotorControl.SchDoc, PCB2.PcbDoc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]
2016-02-26 pouet tp3
    [MotorControl.SchDoc, PCB1_a.PcbDoc, PIC.SchDoc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]
2016-03-04 TP3 document de fabrication update
    [PCB1_a.CSV, PCB1_a.PcbDoc, PIC.SchDoc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]
2016-03-08 tp 3 update pcb
    [PCB1_a.PcbDoc, PIC.SchDoc, PcbLib1.PcbLib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]
2016-03-10 TP3 card rebuilt
    [PcbLib1.PcbLib, toto.PcbDoc]
2016-03-15 tp 3 update output + footprints
    [PcbLib1.PcbLib, TP_2.PrjPcb, power.SchDoc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]
2016-03-16 TP3 output done
    [Bill of Materials-TP_2.xlsx, PcbLib1.PcbLib, Pick Place for PCB1_a.csv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]
2016-04-12 prototype motor control schematic done
    [Autobot_project.PrjPcb, Motor_Control.SchDoc, PCBLIB_Autobot.PcbLib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]
2016-04-18 PIC_Zone creatino + PIC schemalib
    [Autobot_project.PrjPcb, Motor_Control.SchDoc, PIC_Zone.SchDoc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]
2016-04-19 UART update
    [Autobot_project.PrjPcb, Motor_Control.SchDoc, PCBLIB_Autobot.PcbLib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]
2016-04-22 Mic schematic addition
    [Autobot_project.PrjPcb, Bill of Materials-Autobot_project-V1.xlsx, Bill of Materials-Autobot_project.xlsx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]
2016-04-24 UART working
    [Bill of Materials-TP_2.xlsx, Bill of Materials.xls, MicroAmp.SchDoc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]
2016-04-25 BOM update
    [Bill of Materials-Autobot_project-V1.xlsx, Bill of Materials-Autobot_project-V2.xlsx]
2016-04-26 UART put_log
    [Bill of Materials-Autobot_project-V2.xlsx]
2016-04-27 PWM testing WIP
2016-04-28 PWM Working
2016-05-03 Schematic update for l298 - PIC connection
    [MotorControl.SchDoc, PICZone.SchDoc]
2016-05-07 Motor control OK
2016-05-11 PLU C LON PLU C BON
    [Autobot_project.PrjPcb, Bill of Materials-Autobot_project-V1.xlsx, Bill of Materials-Autobot_project-V2.xlsx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]
2016-05-13 footprints ok
    [MIC.SchDoc, PCBLIB_Autobot.PcbLib, PICZone.SchDoc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]
2016-05-13 new on/off alim button
    [MIC.SchDoc, MotorControl.SchDoc, PCBLIB_Autobot.PcbLib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]
2016-05-16 PCB WIP
    [Autobot_project.PrjPcb, MIC.SchDoc, MIC2.SchDoc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]
2016-05-17 bus working
    [Autobot_project.PrjPcb, MIC.SchDoc, MicsBus.SchDoc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]
2016-05-17 additional BOM + PCB update
    [Autobot_project.PrjPcb, Bill of Materials-Autobot_project-Addition1.xlsx, Bill of Materials-Autobot_project.xlsx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]
2016-05-18 schematic update with power source change for Amp
    [MIC.SchDoc, PCBLIB_Autobot.PcbLib, PCB_Autobot.PcbDoc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]
2016-05-20 PCB update, size ok
    [MIC.SchDoc, MicsBus.SchDoc, MotorControl.SchDoc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]
2016-05-21 pcb ok text to place correctly
    [MIC.SchDoc, MicsBus.SchDoc, PCBLIB_Autobot.PcbLib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]
2016-05-22 PCB + output jobs
    [PCBLIB_Autobot.PcbLib, PCB_Autobot.PcbDoc]
2016-05-24 PCB update with new regulator
    [PCBLIB_Autobot.PcbLib, PCB_Autobot.PcbDoc, PowerSupply.SchDoc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]
2016-05-25 PCB update with changes from Greg comments
    [Autobot_project.PrjPcb, Bill of Materials-Autobot_project.xlsx, MIC.SchDoc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]
2016-06-07 resistances / condensateurs update based on MIC POC working
    [Autobot_project.PrjPcb, Bill of Materials-Autobot_project.xlsx, MIC.SchDoc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]
2016-06-10 test microphone ADC initialisation WIP
2016-06-12 ADC working with 16 words buffer on 1 input pin
2016-06-14 final BOM addition
    [Bill of Materials-Autobot_project-Final-V1.xlsx, Bill of Materials-Autobot_project.xlsx]
2016-06-17 new code for PWM control
2016-06-18 conf bits update + PWM ON
2016-06-19 DMA paired with ADC
2016-06-20 chained DMA ok with 3 ADC channels
    [Bill of Materials-Autobot_project-Final-V1.xlsx, Bill of Materials-Autobot_project-Final-V2.xlsx]
2016-06-22 MIC divider bridge update
    [MIC.SchDoc]
2016-06-24 MIC schematic update
    [MIC.SchDoc]
2016-06-27 Clock to 48Mhz and input button interruption ok
2016-06-28 UART bug to solve
    [Button.c, Logging.c, main.c]
2016-06-28 UART problem solved (tx interrupt misunderstanding)
    [Logging.c]
2016-06-29 adc testing
2016-06-29 Motor with delay ok
2016-06-29 ADC WORKING WITH DMA
2016-07-04 mics actions ok, mode switch ok, button actions ok, bumper ok
